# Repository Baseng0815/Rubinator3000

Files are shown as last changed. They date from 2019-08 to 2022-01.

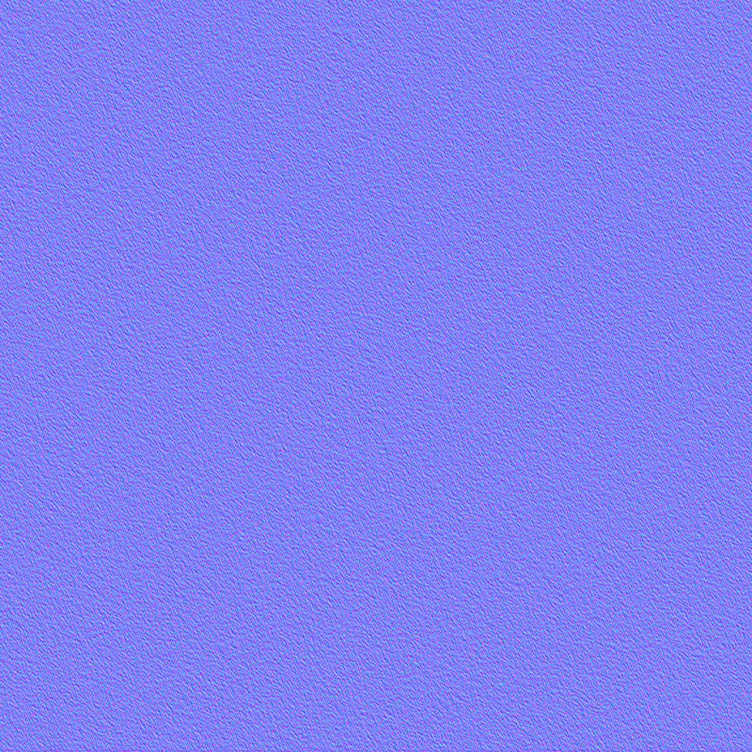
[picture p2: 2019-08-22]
RubinatorTabletView/Assets/Textures/NormalMap.png

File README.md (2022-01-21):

##### GYMNASIUM EDERTALSCHULE, FRANKENBERG-HESSEN

# Jugend forscht 2020

```
Philipp Geil, 19 Jahre
Tim Depner, 18 Jahre
Bastian Engel, 19 Jahre
```
## Das Lösen eines Zauberwürfels

## - der Rubinator3000 -

Mathematik-Informatik
Projektbetreuer: Oliver Blinn, Edertalschule Frankenberg

## Kurzfassung

Bei unserem Projekt “ _Das Lösen eines Zauberwürfels - der Rubinator3000_ ”
versuchten wir, einen verdrehten Zauberwürfel automatisch zu lösen.
Dazu haben wir Software und Hardware entwickelt, die einen Würfel erkennen,
verarbeiten und einen Lösealgorithmus anwenden können.
Anforderungen an die Hardware:
● Drehung jeder Seite des Würfels mit Schrittmotoren
● Elektronik zur Steuerung der Motoren
● Kameras zur Erkennung des verdrehten Würfels
Anforderungen an die Software:
● Auswertung der Kamerabilder und programmiertechnische Darstellung des
Würfels
● Lösealgorithmus entwickeln und Lösezüge berechnen
● Lösezüge am Würfel ausführen
...und natürlich das Vereinen aller Hardware-Komponenten in einer Maschine sowie
dessen Kommunikation mit dem Rechner, auf welchem die Steuerungssoftware
mit grafischer Benutzeroberfläche läuft.

## Erfolge:
1. Preis Regionalwettbewerb 2020
SMA Innovationspreis
Qualifikation Landeswettbewerb, der allerdings aufgrund von Corona abgesagt wurde

## 1. Einleitung

#### 1.1 Wieso einen Zauberwürfel lösen?

Unsere Faszination für Zauberwürfel hat vor ungefähr einem Jahr angefangen, als
wir bei einer extrakurrikularen E-Technik-Vorlesung ein YouTube-Video (Q1) sahen,
in dem jemand einen Zauberwürfel in 4.73 Sekunden löst. Da haben wir uns gefragt,
wie so etwas überhaupt möglich ist. Wir haben es als Kinder selbst probiert und
sogar bis zu drei Seiten gelöst bekommen, aber vollständig klappte es nie. Bei
nachfolgender Recherche im Internet sind wir auf Methoden gestoßen, welche von
sogenannten “Speedcubern” verwendet werden, um den Würfel in einer unglaublich
kurzen Zeit zu lösen.
Vertieft wurde unser Interesse weiter durch die unzähligen Variationen des Würfels.
Abseits der bekannten 3x3-Version ist der Zauberwürfel auch in einigen anderen
Größen von 2x2 bis zu 15x15 erhältlich. Dazu gibt es das Drehpuzzle nicht nur in
Hexaeder-Form, sondern auch in anderen polyedrischen Formen, wie beispielsweise
dem Tetraeder. Einige stellen sich sogar der Herausforderung, den Würfel mit nur
einer Hand, mit den Füßen oder mit verbundenen Augen zu lösen.
Wir selbst schaffen es per Hand, den Zauberwürfel in einer Zeit von circa 45
Sekunden zu lösen. Schaffen wir es, diese Zeit mit unserer Maschine zu
unterbieten?

#### 1.2 Gängige Lösemethoden

Die Lösung des Zauberwürfels erfolgt nicht improvisiert, sondern läuft nach einem
strikten Schema. Dies ist notwendig, um bereits gelöste Teile nicht erneut zu
verdrehen. Manche Teile lassen sich zwar ohne Vorkenntnisse lösen, aber den
Hauptteil löst man mit vorher entwickelten und auswendig gelernten Algorithmen und
Methoden, die den Würfel auf eine bestimmte Art und Weise permutieren.
Die am häufigsten verwendeten Lösemethoden sind zum einen die
“Fridrich”-Methode, welche von Jessica Fridrich entwickelt wurde, und zum anderen
die “Layer-by-Layer”-Methode.
Die Fridrich-Methode enthält viele Algorithmen, die man auswendig lernen muss,
welche jedoch eine kurze Lösezeit garantieren, weshalb sie auch von Speedcubern
verwendet wird.
Die Layer-by-Layer-Methode ist einfacher zu erlernen, erfordert aber mehr Züge, was
die Lösezeit natürlich verlängert.

- Kurzfassung
- 1. Einleitung
      - 1.1 Wieso einen Zauberwürfel lösen?
      - 1.2 Gängige Lösemethoden
      - 1.3 Das Ziel der Arbeit
- 2. Vorgehensweise, Materialien und Methode
      - 2.1 Die Position der Farben auf dem Würfel
      - 2.2 Drehungen der Seiten
      - 2.3 Die Lösung des Zauberwürfels
      - 2.3.1 Das weiße Kreuz
      - 2.3.2 Das F2L
      - 2.3.4 Die letzte Seite
      - 2.4 Die Entwicklung der Software
      - 2.5 Die Entwicklung der Hardware
      - 2.6 Der Bau der Hardware
      - 2.7 Die Digitalisierung des Würfels
- 3. Ergebnisse
      - 3.1 Software
      - 3.2 Hardware
- 4. Ergebnisdiskussion
- 5. Zusammenfassung
- 6. Danksagung
- 7. Quellen- und Literaturverzeichnis

Layer-by-Layer-Methode (Q3)
Ausgang Weißes
Kreuz
Weiße
Ecksteine
Mittlere
Schicht
Gelbes
Kreuz
Gelbe
Ecksteine
Ecksteine
drehen
Fridrich-Methode (Q4)
Ausgang Weißes Kreuz “First two
layers” (F2L)
“Orient last
layer” (OLL)
“Permutate
last layer”
(PLL)
Man erkennt, dass die Fridrich-Methode weniger Schritte benötigt. Dadurch wird sie
jedoch auch komplizierter und schwieriger zu erlernen. Die Layer-by-Layer-Methode
erfordert neun verschiedene Algorithmen, während es bei der Fridrich-Methode
schon 78 sind.

#### 1.3 Das Ziel der Arbeit

Wie schon erwähnt, brauchen wir ganze 45 Sekunden, um den Zauberwürfel per
Hand zu lösen und vergessen häufig Algorithmen. Diesen Problemen wollen wir
durch maschinelles Lösen entgegentreten. Motoren können die Drehungen am
Würfel besser koordinieren als wir mit unseren Händen. Außerdem können Rechner
Algorithmen ohne Probleme speichern und ausführen. Besonders beeindruckt hat
uns dabei der Löseroboter von Ben Katz, welcher in der Lage ist, den Würfel in 0.
Sekunden zu lösen (Q5).
Unser Ziel ist es, den Zauberwürfel innerhalb von 30 Sekunden lösen zu können, d.h.
konkret, eine dafür nötige Farberkennung zu entwickeln, eine entsprechende
Lösesoftware zu schreiben und eine Ansteuerung zu bauen, welche diese
Anforderung erfüllen kann.

## 2. Vorgehensweise, Materialien und Methode

#### 2.1 Die Position der Farben auf dem Würfel

Sei die Menge der Seiten des Würfels und die Menge der Flächen einer Seite.
Damit sind die Positionen der einzelnen Flächen auf dem Würfel bestimmt durch:
Um den Würfel darstellen zu können, müssen die Positionen noch durch die Menge
der Farben des Würfels ergänzt werden:
Damit besteht die Darstellung des Würfels aus einem Array der Länge 6, in welchem
die neun Farbwerte für jede Seite gespeichert sind. Das Programm geht davon aus,
dass sich die orange Fläche links befindet und die weiße Fläche oben. Da die
Implementation des Lösungsalgorithmus leichter fällt, wenn man nicht mit den
einzelnen Flächen arbeitet, sondern jene Flächen zu Steinen zusammenfasst,
welche über die Würfelkanten aneinander grenzen, haben wir uns dazu entschieden,
eine Struktur für die Ecksteine (3 Flächen) und eine für die Kantensteine (2 Flächen)
zu erstellen. In diesen Strukturen werden ein Tupel der Farben des Steines sowie ein
Verweis auf den Würfel, zu dem dieser Stein gehört, gespeichert. Die Steine werden
bei der Initialisierung der Cube-Klasse automatisch aus den vorgegebenen
Positionen erstellt, die für jeden Stein festgelegt sind. Die Steine werden durch ihre
Farben charakterisiert, da die Positionen zum einen durch die Indizes des Arrays
festgelegt sind und es zum anderen für den Lösungsalgorithmus nötig ist, die
Position gewisser Steine anhand der Farben zu identifizieren. Diese Positionen
lassen sich durch einen Vergleich der Farben des Steines mit den vorgegebenen
Steinpositionen bestimmen.

#### 2.2 Drehungen der Seiten

Um den Zauberwürfel nun zu lösen oder zu verdrehen, mussten wir also noch eine
Möglichkeit implementieren, um einzelne Seiten des Würfels im Programm zu
drehen. Eine Drehung wird durch die zu drehende Seite und die Anzahl der
Vierteldrehungen (90°) im Uhrzeigersinn festgelegt.
Jeder Move beschreibt eine bestimmte Permutation des Würfels, da zum einen die
Farben auf der jeweiligen Seite, aber auch teilweise die Farben auf den
angrenzenden Seiten vertauscht werden.

Diese beiden Permutationen können jeweils durch Funktionen beschrieben werden:
Betrachtet man die Drehung einer Seite im Uhrzeigersinn, so lässt sich
bestimmen:
Der Funktionswert von _f_ 1 gibt hierbei die neue Position nach der Drehung an:
Die Funktionswerte von lassen sich nicht allgemein formulieren, da abhängig
von der gedrehten Seite ist. Die Relationen von sind im Programm hinterlegt und
werden auf die entsprechenden Seiten angewendet.

#### 2.3 Die Lösung des Zauberwürfels

#### 2.3.1 Das weiße Kreuz

Das weiße Kreuz wird durch ein Objekt der “CrossSolver”-Klasse gelöst. Dazu wird
zuerst ein Pivotelement festgelegt. Bei diesem Element handelt es sich entweder um
einen weißen Kantenstein, der sich bereits richtig auf der weißen Seite befindet und
bei dem sich die meisten Steine in der gewünschten Position befinden, oder um
einen weißen Kantenstein, der sich mit den wenigsten Zügen in die richtige Position
bringen lässt. Um die Anzahl der Züge zu bestimmen, die benötigt werden, um den
Stein relativ zum Pivotelement richtig auszurichten, gibt es eine Methode, die jeden
Stein bewertet und die Anzahl der Züge zurückgibt. Beim Lösen des weißen Kreuzes
bewertet der “CrossSolver” zuerst für jeden Kantenstein, wie viele Züge jeweils
benötigt werden und löst dann den Kantenstein, für den die wenigsten benötigt
werden. Zum Lösen der einzelnen Steine unterscheidet der “CrossSolver” zwischen
vier verschiedenen Fällen:

1. Der Stein befindet sich mit der weißen Fläche auf der weißen Seite, aberdie
    seitliche Farbe stimmt nicht.
2. Der Stein befindet sich mit der weißen Fläche auf der unteren Seite.
3. Der Stein befindet sich auf der mittleren Ebene, also mit keiner Fläche auf
    der oberen oder unteren Seite.
4. Der Stein befindet sich mit der weißen Fläche auf einer der seitlichen Seiten
    (orange, grün, rot, blau) und mit der anderen Fläche auf der oberen oder
    unteren Seite.
Die einzelnen Fälle werden dann durch vorgegebene Algorithmen gelöst.

#### 2.3.2 Das F2L

Das Lösen des F2L funktioniert analog zum Lösen des weißen Kreuzes. Das
Programm orientiert sich hier nun nicht mehr an nur einem Stein, sondern an jeweils
zwei Steinen, die gelöst werden sollen. Dazu bewertet es wieder jedes Steinpaar und
löst jenes, welches die wenigsten Züge benötigt. Diese Berechnung erfolgt
asynchron, um Rechenzeit zu sparen. Danach wird das Paar mit Hilfe von 13
Algorithmen gelöst.

#### 2.3.4 Die letzte Seite

Für das Lösen der letzten Seite sind im Programm Muster und die dazugehörigen
Zugfolgen hinterlegt (57 OLL und 21 PLL). Die Muster für das OLL beziehen sich nur
auf die Anordnung der gelben Flächen. Dazu wird eine Folge von 9 Bits verwendet,
welche die gelbe Seite repräsentiert, und jeweils vier Folgen von je 3 Bits, welche die
3 Flächen der über die Würfelkanten angrenzenden Seiten repräsentieren. Das
Programm vergleicht dann jegliche Muster mit dem Würfel und kann somit die
Zugfolge angeben. Die PLL-Muster sind etwas komplexer als die OLL-Muster, da das
PLL die einzelnen Farben einbezieht. Dazu wird jeder der vier seitlichen Farben eine
Zahl zugeordnet ((orange, 0), (grün, 1), (rot, 2), (blau, 3)). Im Programm sind dann
die Differenzen zwischen den drei Steinen für alle vier Seiten hinterlegt. Mit diesen
Mustern kann daraufhin die Zugfolge bestimmt werden, die zur Lösung des
Zauberwürfels führt.

#### 2.4 Die Entwicklung der Software

Wir haben mithilfe von Visual Studio Community 2019, einer von Microsoft
entwickelten IDE, programmiert. Das Projektmanagement wird dadurch vereinfacht
und der integrierte Designer erlaubt einfache und gute GUI-Erstellung. Da jeder von
uns schon im Voraus Erfahrung mit dieser Entwicklungsumgebung hatte, mussten
wir uns nicht umstellen und der Entwicklungsprozess konnte sofort starten.
Als Programmiersprache entschieden wir uns für C#, um WPF (Windows
Presentation Foundation) nutzen zu können. Das ist eine GUI-Library, mit der viele
Windows-Programme geschrieben werden. Ein großer Vorteil davon ist, dass das
GUI-Design extern in XAML-Dateien definiert und damit vollständig von der Logik
des Programms abgekoppelt ist. Dies ermöglichte uns, die Arbeit besser aufzuteilen.
So kann ein Programmierer am GUI arbeiten, während ein anderer die Logik dazu
schreibt. Die 2D-und 3D-Ansicht des Würfels erstellten wir mit OpenGL, einer
Graphics-Library, die auch in vielen Computerspielen verwendet wird und sehr
weitreichende Funktionen besitzt.

Da wir zu dritt waren und viele Änderungen parallel zusammenkamen, benötigten wir
ein Versionskontrollsystem, um diese zu verwalten und gegebenenfalls bei Bugs
frühere Versionen wiederherstellen zu können. Entschieden haben wir uns für Git,
welches auch industriell verwendet wird. Damit war es kein Problem mehr, Aufgaben
aufzuteilen und zu synchronisieren.

#### 2.5 Die Entwicklung der Hardware

Das CAD-Modell unseres  _“Rubinator3000”_ haben wir mit dem kostenlosen Programm
“FreeCAD” entworfen, da dieses für unsere Anforderungen genügt und wir unser
Projekt kostengünstig gestalten wollten. Zudem war es uns mit FreeCAD möglich, die
Bauteile in das STL-Format zu exportieren, um sie mit einem 3D-Drucker drucken zu
können. Da unsere Hardware fast ausschließlich aus 3D-Druck Bauteilen besteht,
war diese Funktion sehr hilfreich. Die Schaltpläne für die Ansteuerung der
Schrittmotoren erstellten wir mit Eagle. Eagle bietet zudem die Möglichkeit,
Leiterplatten zu designen, um diese bei einem Leiterplattenhersteller anfertigen zu
lassen.
Die Ansteuerung der Schrittmotoren musste über eine Verstärkerschaltung getätigt
werden. Das lag zum einen daran, dass die Schrittmotoren eine Spannung von 12V
benötigen, während der Arduino nur 5V liefert. Zum anderen wird ein sehr großer
Strom benötigt, um die Magnetfelder innerhalb der Schrittmotoren mit Hilfe von
Spulen zu erzeugen.

#### 2.6 Der Bau der Hardware

Wir haben uns für 3D-gedruckte Bauteile
entschieden, da diese eine höhere Präzision
der Mechanik ermöglichten. Unser erster
Prototyp bestand ausschließlich aus Holz
und es kam aufgrund mangelhafter
Genauigkeit der Mechanik zum
sogenannten “Verkantungsproblem”: Eine
Seite des Würfels verkantete sich nach einer
unvollständigen Drehung. Dieses Problem
lösten wir letztendlich durch die zweite
Version der Hardware und einen anderen Zauberwürfel. Zudem ließen die
verwendeten Miniaturbalg-Kupplungen zu viel Spielraum zu, was zu
Ungenauigkeiten bei den Würfeldrehungen führte. Deshalb ersetzten wir sie durch
Elastomerkupplungen, da diese deutlich genauer sind, wodurch sich der Würfel viel
besser drehen lässt.
Zudem haben wir uns Platinen zur Ansteuerung der Schrittmotoren anfertigen
lassen, da die anfangs selbst gelöteten Platinen teilweise unzuverlässig waren und
sehr viel Platz im Gehäuse in Anspruch nahmen. Hinzu kam noch, dass die selbst
gelöteten Platinen viel Wärme entwickelten, da jede einzelne von ihnen einen

separaten Spannungsregler besaß, der für den Anschluss eines Mikrocontrollers
gedacht war.
Im nebenstehenden Bild ist eine
Schaltung abgebildet, welche zeigt,
wie mithilfe des Transistors (T1) der
Stromkreis der Spule des
Schrittmotors (L1) geschlossen wird^1.
Dadurch wird es möglich, dass Strom
fließen kann, welcher das
magnetische Feld im Schrittmotor
erzeugt. Der Basiswiderstand (R1)
dient zur Begrenzung des
Basisstroms des Transistors, da der
Ausgang des Arduino einen Strom
von maximal 40mA zur Verfügung
stellt.
Wir ließen die Bodenplatte bei der Firma Viessmann drucken, weil diese für unseren
3D-Drucker zu groß war. Sie stellte uns für diesen Druck einen besseren 3D-Drucker
zur Verfügung. Nach dem Druck haben wir sie auf eine solide Holzbox gesetzt,
welche auch die Elektronik enthält. Dadurch wird Stabilität garantiert und die Motoren
können passend positioniert werden.

#### 2.7 Die Digitalisierung des Würfels

Unsere erste Methode zur Digitalisierung des Würfels sah folgendermaßen aus:

(^1) Die Freilaufdiode wurde zur Vereinfachung der Schaltung weggelassen

Wir lasen jede einzelne Seite mit der Kamera eines Smartphones ein, um daraus den
Würfel digital zusammensetzen zu können. Dafür haben wir eine Android-App in der
Programmiersprache Java geschrieben.
Ein Computer – also auch das Smartphone, welches wir benutzen – stellt Farben im
RGB-Format dar. Anhand dieser Werte werden die einzelnen Würfel-Farben
(Orange, Weiß, Grün, Gelb, Rot und Blau) auch unterschieden.
Um sich auch wechselnden Lichtverhältnissen anpassen zu können, war es nötig zu
Beginn Referenz-RGB-Werte festzulegen, anhand welcher die App die Farben
unterschied.
Im nächsten Schritt hielten wir die Handykamera vor jede Würfelseite. Die App las
die RGB-Werte der einzelnen Flächen aus und ordnete ihnen anhand der anfangs
eingelesenen Referenz-RGB-Werten die entsprechende Farbe zu.
Sobald die App eine Würfelseite eingelesen hatte, schickten wir dessen Farben über
ein WLAN-Netzwerk an jenen Laptop, auf welchem das Hauptprogramm lief.
Nachdem wir auf diese Weise alle sechs Seiten eingelesen und an den Laptop
geschickt hatten, könnte dieser daraus den Würfel digital zusammensetzen.
Die zweite Version unseres Projekts brachte auch ein Upgrade in der Farberkennung
mit sich. Anstatt mit einer Handy-App jede Seite einzeln einzulesen, brachten wir vier
stationäre USB-Kameras an der Maschine an, mit welchen wir die RGB-Werte der
einzelnen Flächen des Würfels automatisch einlesen. Dies beschleunigt den Prozess
der Digitalisierung des Würfels natürlich enorm.
Auch an der Erfassung und Verarbeitung der eingelesenen RGB-Werte haben wir
Änderungen vorgenommen:
Für jede einzelne Fläche des Würfels
legen wir eine Position auf einem der 4
Kamera-Streams fest, an welcher die
RGB-Werte der jeweiligen Fläche
ausgelesen werden sollen. Da die 8
Mittelsteine des Würfels ihre Position
während des Drehen nie verändern,
werden deren RGB-Werte gar nicht mehr
eingelesen.
So lesen wir alle RGB-Werte an den 48
Positionen ein und berechnen die
jeweilige Wahrscheinlichkeit dafür, dass
die jeweiligen RGB-Werte zu einer orangen, weißen, grünen, gelben, roten oder
blauen Fläche gehören.
Die 8 Flächen an den Positionen mit den höchsten Orange-Wahrscheinlichkeiten
bestimmen wir als orange Flächen. So gehen wir die restlichen 5 Farben ebenfalls
durch und haben zum Schluss 8 Flächen von jeder Farbe, mit welchen wir wiederum
den Würfel digital darstellen.

Durch dieses Verfahren wird die Farberkennung viel präziser, da wir davon
ausgehen, dass wir genau 8 Flächen von allen Farben haben.
Ein Problem, welches wir bei der Farberkennung hatten war Folgendes:
Aufgrund der sehr glatten Oberfläche der Würfelflächen, spiegelten diese das
Umgebungslicht teilweise gebündelt direkt in eine der Kameralinsen. Dadurch war im
Kamerabild nicht die entsprechende Farbe der Seite zu sehen, sondern ein helles,
weißliches Leuchten. Dies verfälschte die RGB-Werte, welche für die dazugehörige
Fläche eingelesen wurden. Eine eigentlich blaue Fläche erschien somit
unerwünschterweise weiß. Wir haben dieses Problem gelöst, indem wir einen
Vorhang über die ganze Maschine gehängt haben, um den Spiegelungseffekt zu
minimieren. Damit wir jedoch überhaupt noch etwas mit den Kameras sehen können,
haben wir zusätzlich LEDs direkt in die Maschine gebaut, welche den Würfel mit
diffusem Licht bescheinen.
Dies soll jedoch nur vorübergehend die Lösung des Problems sein, da das Abdecken
und das Entfernen der Abdeckung recht viel Zeit braucht. Für die Zukunft planen wir,
nicht absolute Positionen, an welchen die Farben des Würfels ausgelesen werden,
zu benutzen. Stattdessen soll das Programm mittels Konturerkennung selbst
herausfinden, wo sich auf dem entsprechenden Kamerabild die einzelnen
Würfel-Flächen befinden, von welchen das Programm daraufhin die entsprechenden
Farben ausliest. Hierbei könnten wir zu helle Pixel aussortieren, wodurch das
“Spiegelungs-Problem” gelöst würde. Erste Tests in separat von uns programmierten
Anwendungen liefern vielversprechende Ergebnisse. Jetzt gilt es noch, die neue
Farberkennung in das Hauptprogramm zu implementieren.

## 3. Ergebnisse

#### 3.1 Software

Wir haben mithilfe der vorgestellten Vorüberlegungen und Methoden das
Hauptprogramm fertiggestellt, welches den Würfel lösen und die Lösealgorithmen
über eine serielle Schnittstelle an den Arduino schicken kann.
Die Effizienz der Algorithmen lässt sich an folgendem Graph ablesen:
Für jede Verdrehungsanzahl machten wir 30
Testdurchgänge, woraufhin daraus der
Mittelwert gebildet wurde. Die
Schwankungen lassen sich dadurch erklären,
dass nur ein einziger zusätzlich ausgeführter
Algorithmus mehrere Züge enthält und
dadurch das Ergebnis stark beeinflusst
werden kann.
Es ist zu erkennen, dass unsere Lösung ab
vier Verdrehungen erheblich mehr Züge
benötigt. Ab sechs Verdrehungen pendelt sich
die Anzahl der Lösezüge auf ungefähr 65 ein.
Die Schrittmotoren lassen sich mit 360° pro Sekunde drehen, was zwei Zügen
entspricht. Daher ist eine theoretische Lösezeit von ca. 15 Sekunden erreichbar, die
aber durch Ausnahmefälle wie zum
Beispiel die Doppeldrehung einer
Seite oder dem  _Multiturning_
Schwankungen unterliegt.
Außerdem ist zu erkennen, dass
der Zugzuwachs am stärksten vom
FTL beeinflusst wird, wobei die
OLL- und PLL-Algorithmen gegen
Ende weniger beitragen. Das Kreuz
hat kaum Einfluss.
Die grafische Oberfläche des
Programms enthält alle nötigen
Kontrollelemente, so zum Beispiel
das Verdrehen oder Lösen des Würfels oder Debug-Fenster zum Beheben von
fehlerhaften Algorithmen und Mustern. Dadurch können wir leicht und ohne

ständiges Überlegen Einstellungen ändern und Tests durchführen. Das ist zum
Beispiel besonders relevant für die Verbindung zum Mikrocontroller, da diese über
einen sich ändernden COM-Port stattfindet, welchen man anfangs auswählen muss.

#### 3.2 Hardware

Der Arduino wartet nach dem Verbinden mit dem Programm auf die Befehle und
führt diese aus. Er ist nötig, da die Schrittmotoren nicht direkt an den Computer
angeschlossen
werden können.
Zudem benötigen die
Schrittmotoren sehr
viel Strom. Deshalb ist
es notwendig, für
jeden Schrittmotor
eine Schaltung zu
bauen, die genug
Strom liefern kann,
um den Würfel zu
drehen. Anfangs
hatten wir die Motoren
nach einer Drehung
nicht abgeschaltet und
so entstand das
Problem, dass alle
inaktiven Motoren zu

viel Strom verbrauchten und somit nicht genug Drehmoment bereitstand, um den
Würfel zu drehen. Dieses Problem haben wir softwaretechnisch gelöst, indem wir
den Strom der Motoren nach jeder Drehung abschalteten und so der komplette
Strom des Netzgerätes für einen oder bei Multiturns zwei Motoren bereitsteht.

## 4. Ergebnisdiskussion

Unser  _“Rubinator3000”_ ist noch nicht das perfekte Ergebnis jahrelanger Forschung,
aber es kann sich trotzdem sehen lassen.
Wie anfangs bereits erwähnt, kam uns die Idee zum Bau einer solchen Maschine, bei
einer extrakurrikularen E-Technik-Vorlesung im Rahmen der Young Engineer
Academy (YEA). Wir haben dort überlegt, was wir als unser Abschlussprojekt bei der
YEA realisieren könnten. Da wir noch viel Zeit hatten, bis das Projekt vorgestellt
werden sollte, entschieden wir uns nach einigen Suchanfragen im Internet für den
Bau eines doch recht aufwendigen Zauberwürfel-Lösers. Einige weitere
Kursteilnehmer, welche sich ebenfalls für den Zauberwürfel begeistern, unterstützten
unsere Idee.
Anfangs schien unsere Aufgabe recht simpel, da man lediglich 6 Schrittmotoren
benötigte, die die Seiten des Zauberwürfels drehen sollten.
Bereits in den nächsten Wochen (Januar 2019) starteten wir mit der
Programmierung. Der eigentliche Bau der ersten Maschine begann dann Ende April
2019 und pünktlich zum Präsentationstermin am 28. Juni vollendeten wir die erste
Version der Hardware. Bis dahin hatten wir während der Schulzeit schon dutzende
Freistunden in unser Projekt investiert, da die Umsetzung des Projekts dann doch
komplizierter war, als wir zunächst vermutet hatten. Vor allem die Drehung des
Würfels machte uns zu schaffen, da die Hardware zu ungenau war und der Würfel
sich deshalb immer wieder verkantete. Dies war aber letztendlich nicht das größte
Problem, welches wir bei der Präsentation hatten.
Auf der Bühne scheiterte die Vorführung unserer Maschine am Lösen des
Zauberwürfels durch das Programm.
Also entschlossen wir uns, in den Sommerferien das Programm zu überarbeiten. Da
der bestehende Code mittlerweile sehr unübersichtlich war und wir nicht genau
wussten, wo die einzelnen Fehler lagen, entschlossen wir uns dazu, das Programm
von Grund auf neu zu entwickeln. Wir besaßen bereits das Vorwissen aus dem
ersten Versuch , weshalb uns die Entwicklung der zweiten Maschine leichter fiel.
Aufgrund der Verkantungen des Würfels kam uns die Idee, die Teile der Hardware,
welche eine hohe Genauigkeit erforderten, mit dem 3D-Drucker zu fertigen, da dieser
viel genauere Ergebnisse liefert als das Aussägen aus Holz. Zudem haben wir neue
Kupplungen eingebaut, die zur Erhöhung der Genauigkeit beitrugen.

Das Projekt erschien uns auf den ersten Blick leicht, aber es gab viele Faktoren, die
wir nicht berücksichtigt hatten. Darunter fiel zum Beispiel das Einlesen des Würfels,
das Bauen der Hardware mit einer hohen Genauigkeit und vieles andere.
Die Software könnte noch verbessert werden, indem man beispielsweise eine andere
Methode zum Lösen des Würfels verwendet, die weniger Züge benötigt. Diese
Verbesserung würde das maschinelle Lösen auch erheblich beschleunigen, da sich
die Motoren dadurch weniger drehen müssten.
Zudem könnte man auch Motoren verwenden, die sich schneller ansteuern lassen,
welche ebenfalls das Lösen beschleunigen würden.
Wir hatten während der Entwicklung die Idee das Hauptprogramm auf einem
Raspberry Pi laufen zu lassen, da dieser den Computer ersetzen würde, der die
Lösung berechnet. Diese Idee verwarfen wir aber schnell, da wir schon angefangen
hatten, die Software auf dem .NET Framework von Microsoft für Windows zu
entwickeln, während der Raspberry auf einem linuxbasierten Betriebssystem läuft.
Der Ansatz könnte aber in der Zukunft realisiert werden.
Auch die Ansteuerung der Motoren hat uns Probleme bereitet, da wir eine eigene
Platine entwickelt und einen Mikrocontroller programmiert haben. Dieser ist jedoch
beim Debuggen der Software durch eine Überspannung kaputt gegangen und wir
mussten ihn durch einen Arduino ersetzen.

## 5. Zusammenfassung

Zusammenfassend lässt sich sagen, dass unser Projekt noch viele
Erweiterungsmöglichkeiten bietet. Es könnten beispielsweise noch LEDs eingebaut
werden, die für eine bessere Beleuchtung des Würfels bei schlechten
Lichtverhältnissen sorgen.
Unser Ziel, dass unsere Maschine weniger Zeit zum Lösen des Würfels benötigt als
wir selbst per Hand, hat das Projekt noch nicht ganz erreicht. Es befindet sich aber
auf einem guten Weg zu einer Lösung, die unseren ursprünglichen Anforderungen
gerecht wird. Dies könnte durch weitere Verbesserungen der Hard- und Software
erreicht werden.
Das Projekt  _“Rubinator3000”_ hat zwar nur einen kleinen Nutzen für die Allgemeinheit,
aber es hat uns geholfen, unsere Kompetenzen im Bereich der Programmierung und
der Entwicklung von Hardware zu erweitern. Zudem haben wir die Erfahrung
gemacht, dass Dinge und Ideen oft einfacher erscheinen, als sie es eigentlich sind.
Es lohnt sich also, zuerst darüber nachzudenken, wie man sie angeht und realisiert.
Zuletzt durften wir die Erfahrung machen, was man mit Teamwork alles erreichen
kann. Während des Entwicklungsprozesses haben sich alle Team-Mitglieder nur auf

jeweils ein Teilgebiet spezialisiert. Trotzdem können wir durch unsere gelungene
Zusammenarbeit nun einen voll funktionsfähigen Zauberwürfellöser präsentieren.

## 6. Danksagung

Abschließend bedanken wir uns für jegliche Unterstützung während der Umsetzung
unseres Projekts.
Exemplarisch möchten wir hier die Fachschaft Physik der Edertalschule nennen,
welche uns bei Fragen in der Umsetzung beriet und uns kostenlos über einen
längeren Zeitraum den Zugang zu ihrem Werkraum gewährte, in welchem wir unsere
Maschine entwickeln und anfertigen konnten. Zudem danken wir unseren
Mitschülern der Young Engineer Academy, die uns beim Bau der ersten Version des
“Rubinator3000” unterstützt haben.
Darüber hinaus geht ein riesiges Dankeschön an die Viessmann Group, welche uns
finanziell bei der Anfertigung der Hardware unterstützte. Zusätzlich ermöglichte sie
uns die Teilnahme an der Young Engineer Academy, durch welche wir essentielle
Grundkenntnisse und letztendlich auch die Idee für dieses Projekt bekommen haben.

## 7. Quellen- und Literaturverzeichnis

##### Q1: 04.01.2020 16: https://www.youtube.com/watch?v=KfpJZHP6DLA
##### Q2: 04.01.2020 17: https://speedcube.de/
##### Q3: 04.01.2020 17: https://ruwix.com/the-rubiks-cube/how-to-solve-the-rubiks-cube-beginners-method/
##### Q4: 04.01.2020 17: https://ruwix.com/the-rubiks-cube/advanced-cfop-fridrich/
##### Q5: 04.01.2020 17: https://www.youtube.com/watch?v=nt00QzKuNVY
##### Q6: 14.01.2020 19: https://www.arduino.cc/en/Tutorial/DigitalPins

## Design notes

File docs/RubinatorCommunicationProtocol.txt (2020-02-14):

A0xbyte		meaning

state:
0xA1		disconnect
0xA2		connect
0xA3		solve
0xF1		disconnected
0xF2		connected
0xF3		solved

bluetooth:
0x00		transmit cube to client
0x01		transmit cube to server
0x30		solve cube
0x31		shuffle cube

LED control:
0x41		LED's down          0b0100_0001
0x43		LED's up            0b0100_0010
0x44		LED stripes         0b0100_0100

errors:
0xB0		error
0xB1		error not connected
0xB2		error not valid

moves:
0x02		Move 'L'
0x03		Move 'Li'
0x04		Move 'U'
0x05		Move 'Ui'
0x06		Move 'F'
0x07		Move 'Fi'
0x08		Move 'D'
0x09		Move 'Di'
0x0A		Move 'R'
0x0B		Move 'Ri'
0x0C		Move 'B'
0x0D		Move 'Bi'

parallel moves:
0x10		Move 'LR'		0b0001_0000
0x11		Move 'LRi'		0b0001_0001 
0x12		Move 'LiR'		0b0001_0010
0x13		Move 'LiRi'		0b0001_0011
0x14		Move 'UD'		0b0001_0100
0x15		Move 'UDi'		0b0001_0101
0x16		Move 'UiD'		0b0001_0110
0x17		Move 'UiDi'		0b0001_0111
0x18		Move 'FB'		0b0001_1000
0x19		Move 'FBi'		0b0001_1001
0x1A		Move 'FiB'		0b0001_1010
0x1B		Move 'FiBi'		0b0001_1011

0x20 + "Move"	Move "Move" done

states:

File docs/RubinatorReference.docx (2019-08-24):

Rubinator

Inhalt:

1. Das weiße Kreuz
2. FTL
1. Das weiße Kreuz
  1.1. Mögliche Stellung der weißen Kantensteine
1. Kantenstein in der gelben Ebene
  a. Weiße Fläche zeigt nach oben (gelbe Seite)
  b. Weiße Fläche zeigt zur Seite
2. Kantenstein in der mittleren Ebene
  a. Weiße Fläche zeigt zur Seite
3. Kantenstein in der weißen Ebene
  a. Weiße Fläche zeigt nach unten (weiße Seite)
  b. Weiße Fläche zeigt zur Seite

Daraus ergeben sich 5 mögliche Fälle, die auftreten und unterschiedlich gelöst werden.

  1.2. Lösung der Stellungen
    1.2.1. Kantenstein auf der gelben Ebene
  a. Weiße Fläche zeigt nach oben
1. Den weißen Kantenstein solange auf der gelben Ebene bewegen (U) bis er die entsprechende Seite erreicht hat.
2. Die Seite, auf der der Kantenstein eingesetzt wird, wird zwei Mal gedreht, sodass der weiße Kantenstein auf der weißen Ebene ist.
  b. Weiße Fläche zeigt zur Seite
1. Die gelbe Ebene solange drehen bis der weiße Kantenstein die entsprechende Seite erreicht hat.
2. Die entsprechende Seite um 90° im Uhrzeigersinn drehen und die weiße Seite danach ebenfalls im Uhrzeigersinn drehen.
3. Die benachbarte Seite gegen den Uhrzeigersinn drehen, um den Kantenstein auf die weiße Ebene zu befördern.
4. Die weiße Ebene gegen den Uhrzeigersinn zurück in die ursprüngliche Position drehen.
1. Weißer Kantenstein in der mittleren Ebene
1. Die weiße Ebene so drehen, dass der Kantenstein eingesetzt werden kann
2. Den Kantenstein einsetzen
3. Die weiße Ebene zurück in die ursprüngliche Position drehen
2. Weißer Kantenstein in der weißen Ebene
  a. Weiße Fläche zeigt nach unten
1. Seitliche Seite im Uhrzeigersinn drehen
2. Die weiße Ebene ausrichten
3. Den Kantenstein einsetzen
4. Die weiße Ebene zurückdrehen
  b. Weiße Fläche seitlich
1. Seitliche Seite drehen
2. Die weiße Ebene ausrichten
3. Den Kantenstein einsetzen
4. Die weiße Ebene zurückdrehen
2. FTL
  2.1. Weißen Eckstein in einen Slot positionieren

Der Stein wird in den richtigen Slot gesetzt, wenn er in einem Zug dort positioniert werden kann. In dem anderen Fall wird er in einen beliebigen Slot positioniert und danach mit dem Kantenstein gepaart, bevor er dann in den richtigen Slot gesetzt wird.

Mögliche Fälle:

1. Der Eckstein und der entsprechende Kantenstein sind bereits gepaart
2. Die weiße Fläche des Ecksteins zeigt zur Seite
3. Die weiße Fläche zeigt nach oben
  2.2. Lösung
    2.2.1. Fall 1

Die beiden Steine werden in den richtigen Slot eingesetzt

    2.2.2. Fall 2
1. Weiße Fläche wird auf die Seite gedreht, die der Gegenfarbe der seitlichen Seite des Ecksteins entspricht.
2. Die Seite der seitlichen Farbe wird gedreht (weiße Fläche auf Tile 8 → gegen den Uhrzeigersinn, weiße Fläche auf Tile 6 → im Uhrzeigersinn)
3. Gelbe Seite drehen (weiße Fläche auf Tile 6 → gegen den Uhrzeigersinn, weiße Fläche auf Tile 8 → im Uhrzeigersinn)
4. Die Seite der seitlichen Farbe zurückdrehen
    2.2.3. Fall 3

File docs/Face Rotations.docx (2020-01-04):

Face Rotations

L-Move

f_0 :{{t∈(U∩{0;3;6})}→Ft⟼t

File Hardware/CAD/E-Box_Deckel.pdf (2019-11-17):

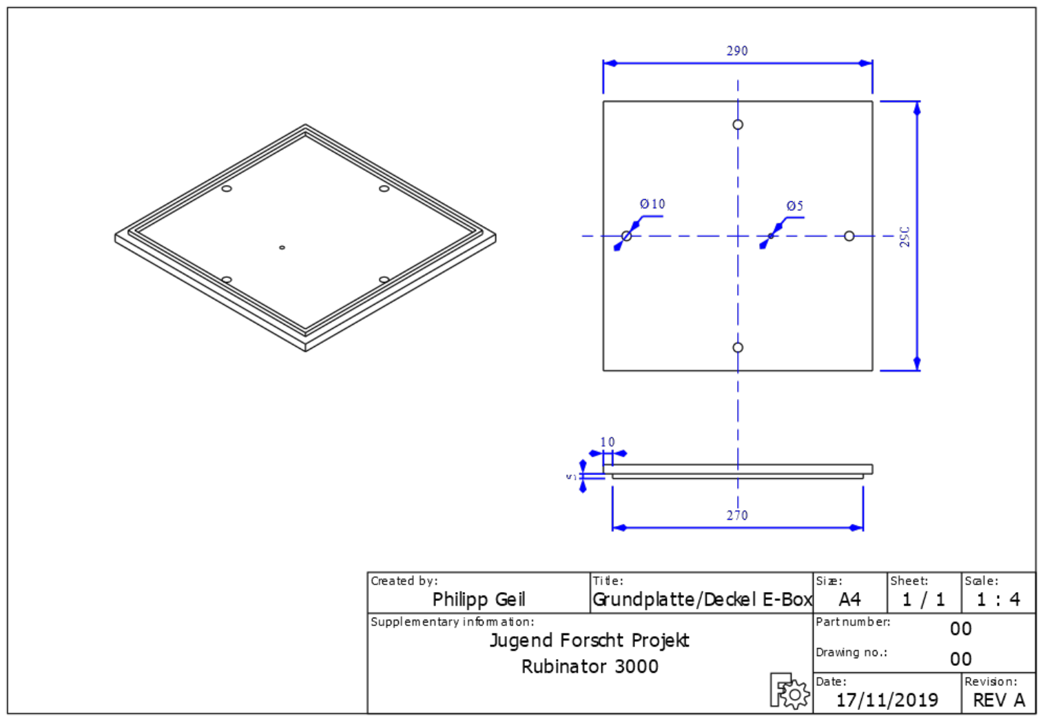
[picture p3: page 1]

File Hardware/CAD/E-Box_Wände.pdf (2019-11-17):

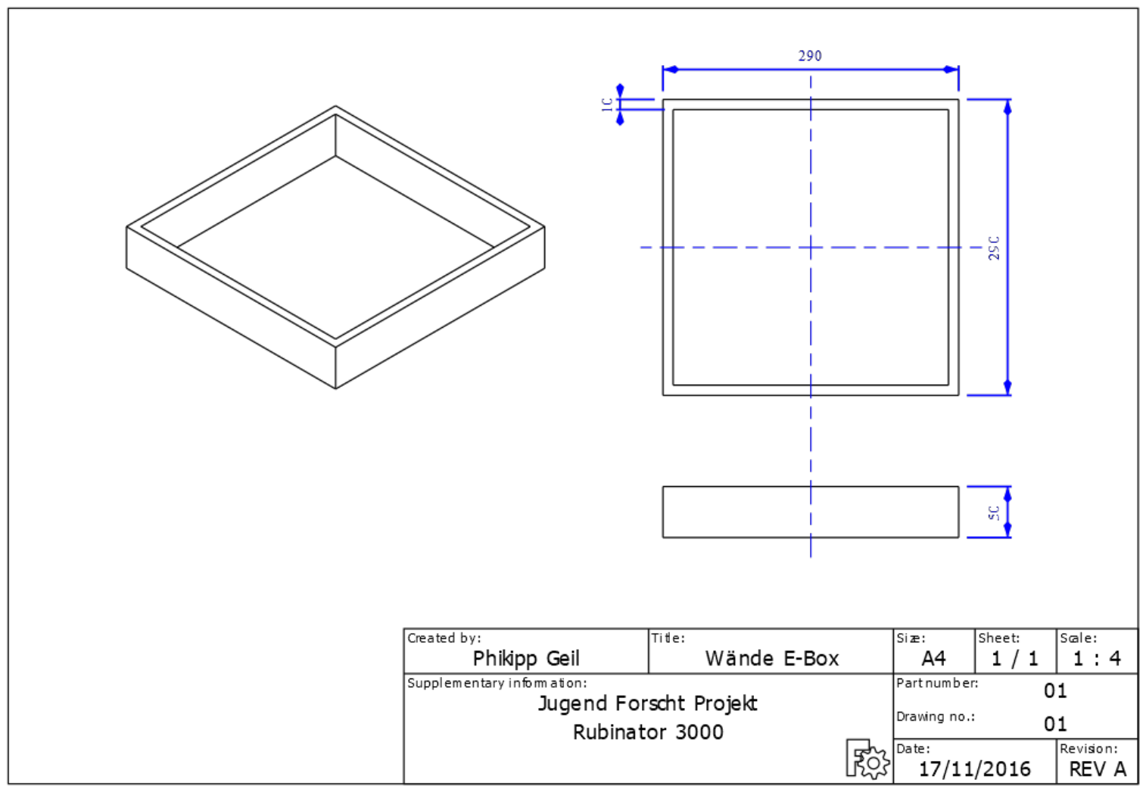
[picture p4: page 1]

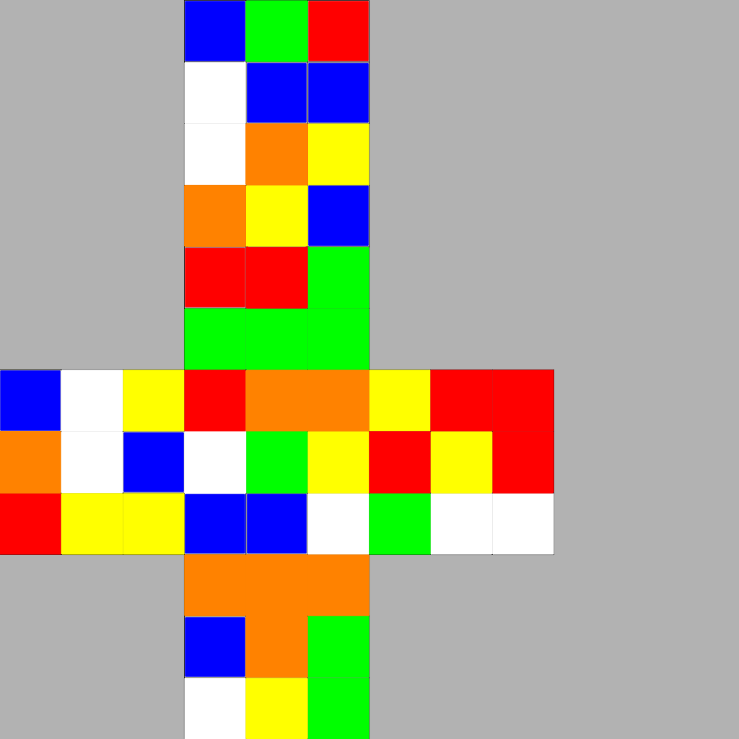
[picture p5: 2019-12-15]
Hardware/CAD/blender/CubeTex.png

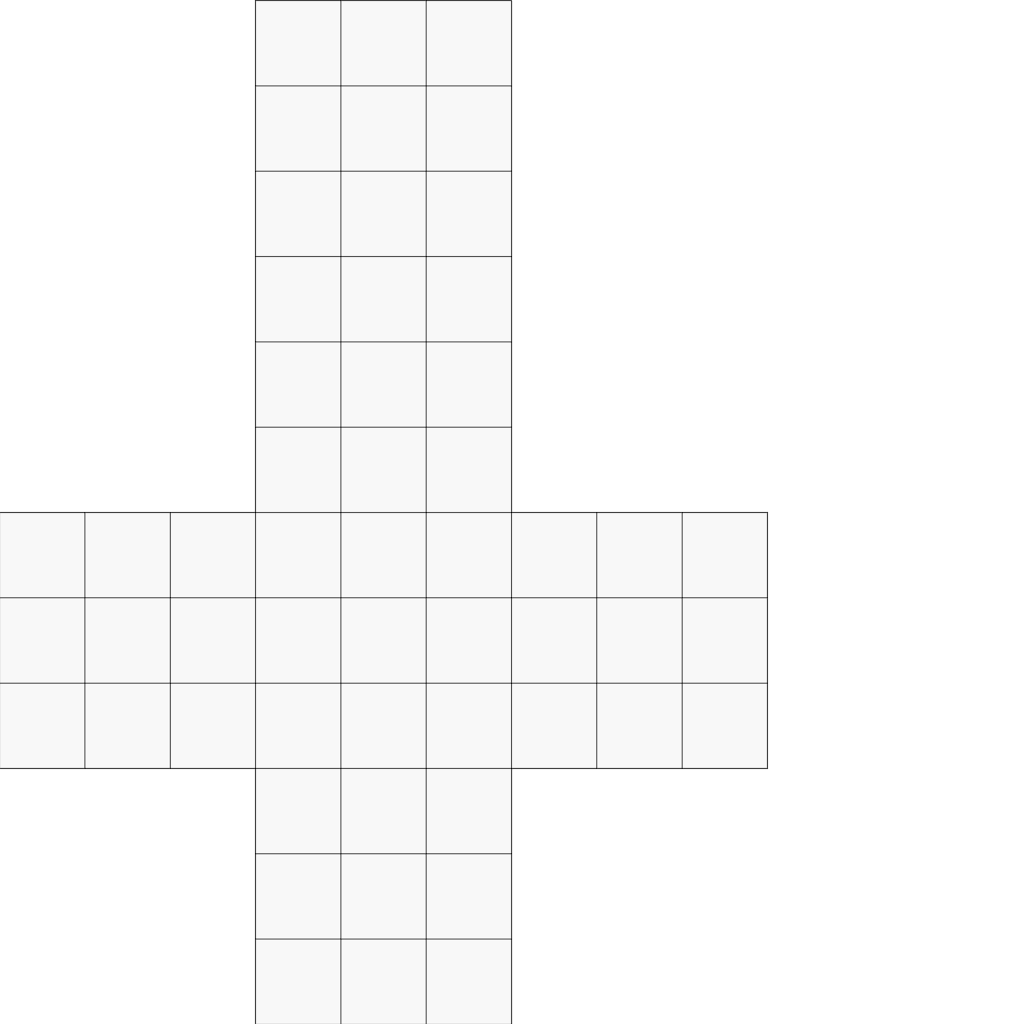
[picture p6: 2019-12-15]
Hardware/CAD/blender/uvs.png

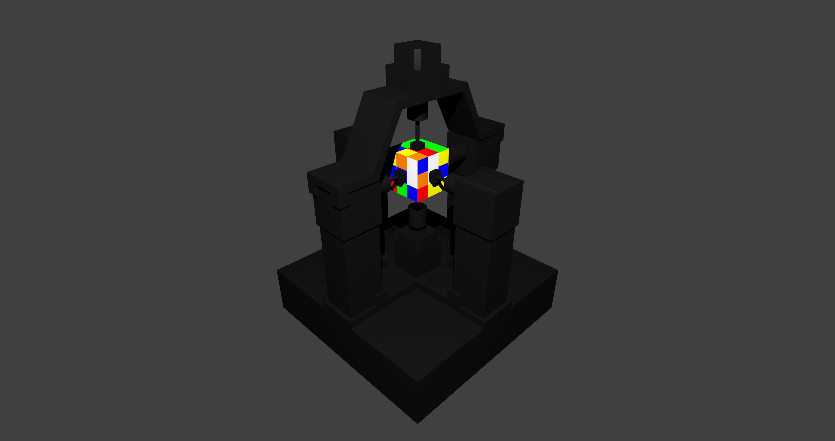
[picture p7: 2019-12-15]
Hardware/CAD/blender/Rubinator3000.png

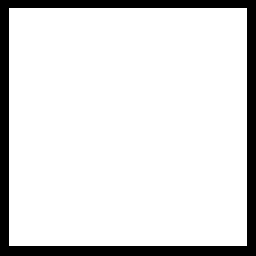
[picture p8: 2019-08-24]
RubinatorTabletView/Assets/Textures/BlendFrameThick.png

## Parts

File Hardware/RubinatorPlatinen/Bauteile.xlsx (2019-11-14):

Teil | Anzahl | Vorhanden
ATMega16-P + IC-Sockel | 1 | 1
Festspannungsregler 5V | 1 | 1
Festspannungsregler 3.3V | 1 | 1
Widerstände
100Ω | 1 | 1
200Ω | 30 | 30
PinHeader (female)
1x4 | 6 | 6
2x8 | 1 | 1
2x10 | 1 | 1
PinHeader (male)
2x10 | 1 | 1
Dioden 1N4446 | 24
Dioden 1N4148 | 2
Transistoren NPN groß | 24 | 24
Transistoren NPN klein | 3 | 3

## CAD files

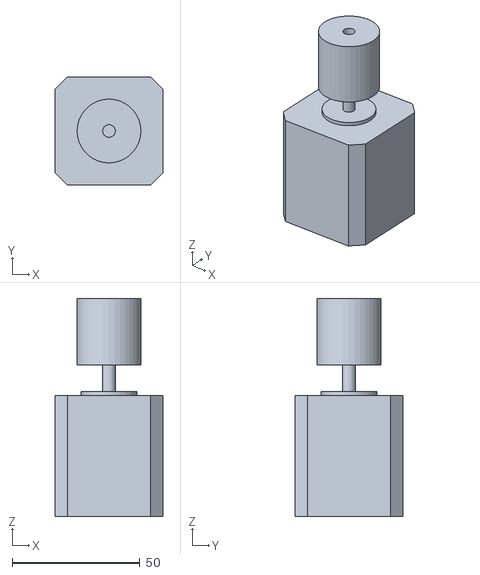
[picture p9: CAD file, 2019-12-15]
Hardware/CAD/AntriebUnten.stl
42.5 x 42.5 x 85.4

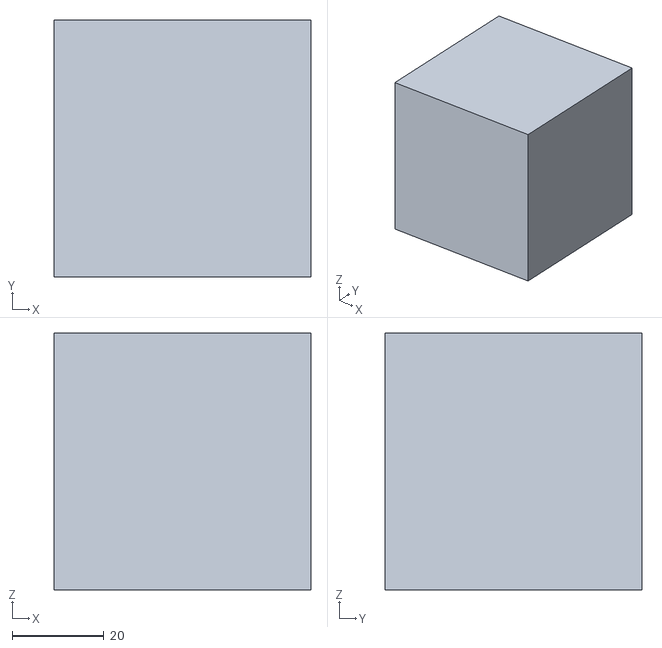
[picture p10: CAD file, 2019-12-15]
Hardware/CAD/blender/Würfel.stl
56.0 x 56.0 x 56.0

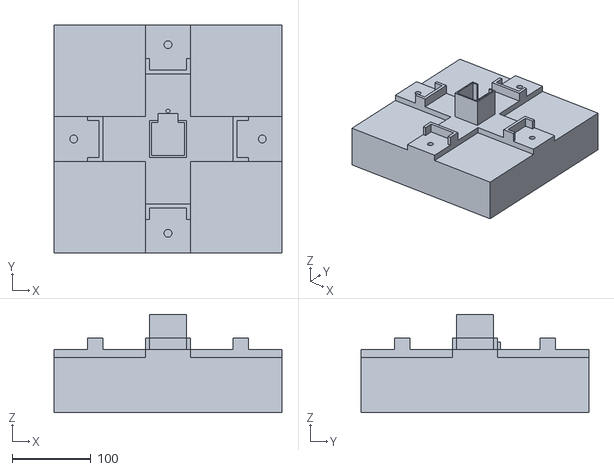
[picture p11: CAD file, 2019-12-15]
Hardware/CAD/blender/Elektrobox.stl
290.0 x 290.0 x 125.0

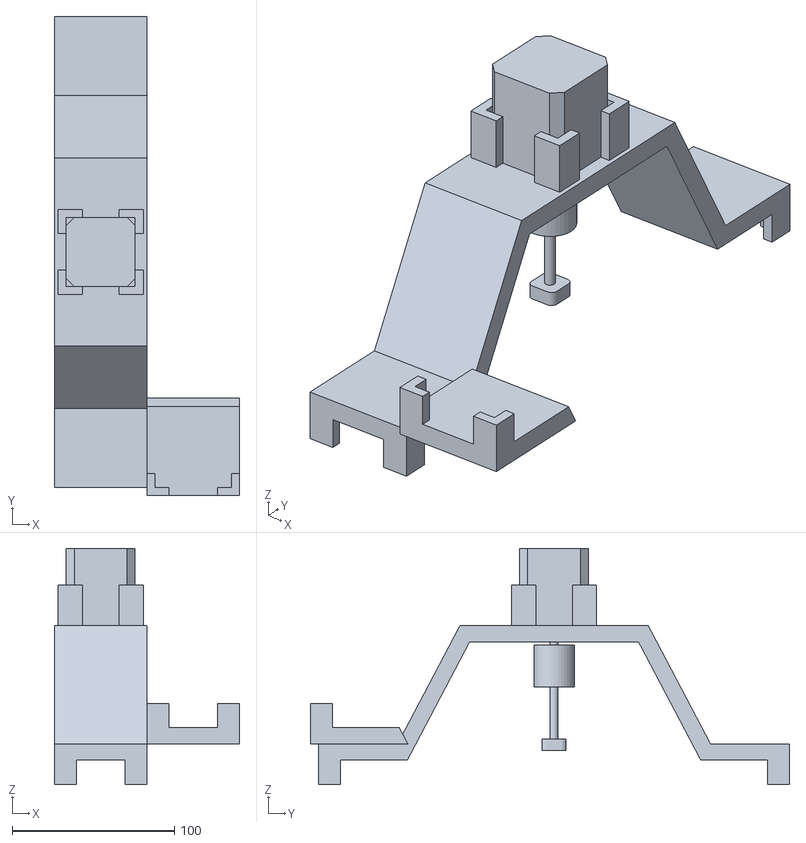
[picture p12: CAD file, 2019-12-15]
Hardware/CAD/blender/HalterungOben.stl
114.0 x 295.0 x 145.2

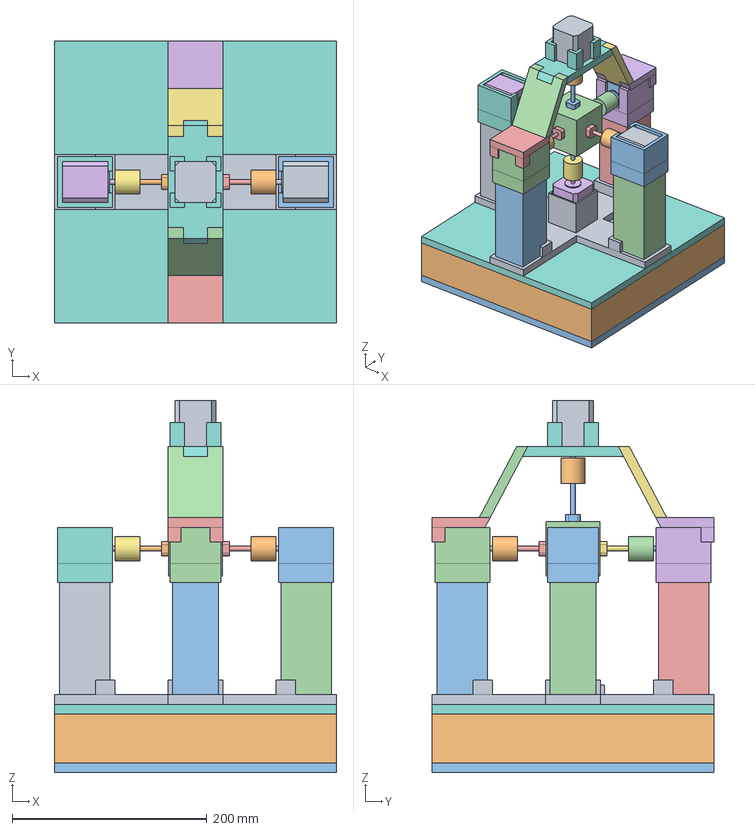
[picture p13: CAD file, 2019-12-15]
Hardware/CAD/Rubinator3000.FCStd
290.0 x 290.0 x 382.3 mm
MotorVorne
KupplungVorne
StützeVorne
MotorufsatzVorne
VerbindungVorne
MotorUnten
KupplungUnten
VerbindungUnten
MotorRechts
KupplungRechts
MotorufsatzRechts
StützeRechts
VerbindungRechts
MotorLinks
KupplungLinks
MotorufsatzLinks
StützeLinks
VerbindungLinks
MotorHinten
KupplungHinten
StützeHinten
MotorufsatzHinten
VerbindungHinten
Deckel
Bodenplatte
Wände
Grundplatte
MotorOben
KupplungOben
VerbindungOben
Würfel

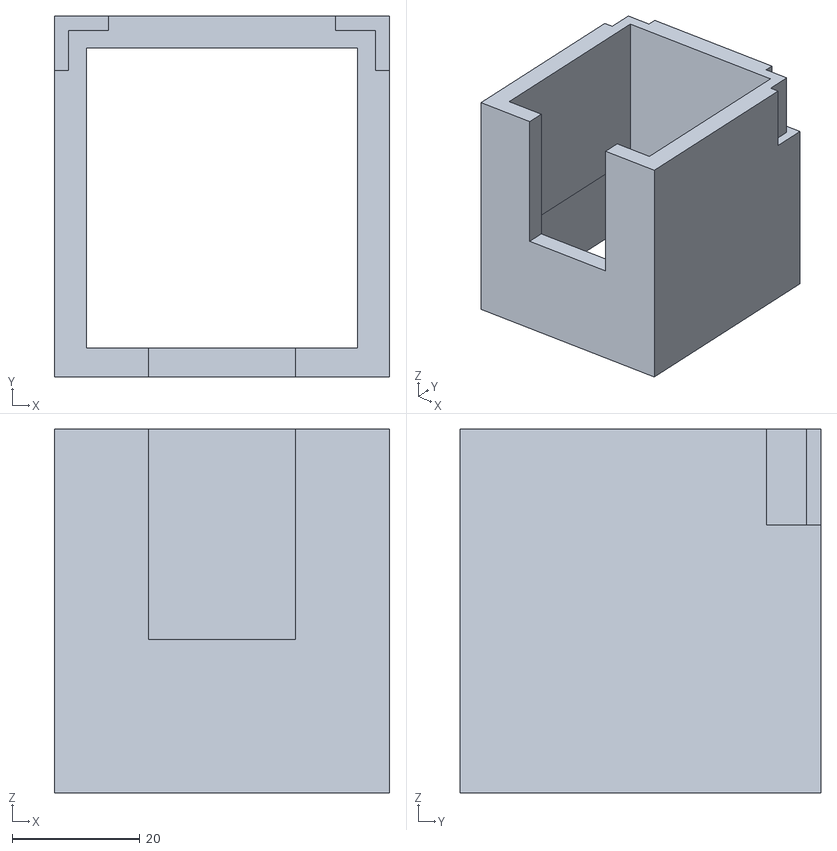
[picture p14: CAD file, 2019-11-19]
Hardware/CAD/AufsatzMotorAussparung.stl
52.5 x 56.5 x 57.0

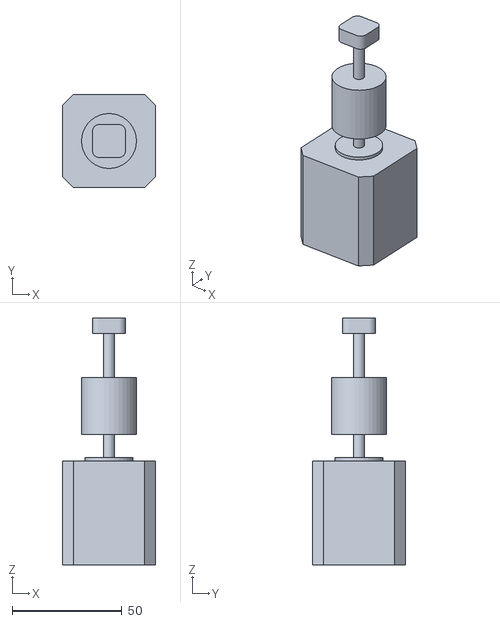
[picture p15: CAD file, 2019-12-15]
Hardware/CAD/blender/Antriebuten.stl
42.5 x 42.5 x 112.4

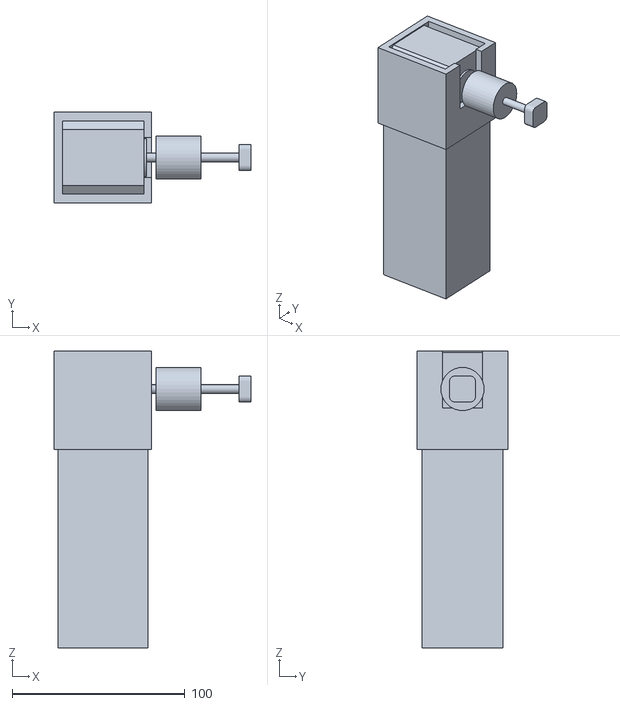
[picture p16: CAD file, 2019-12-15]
Hardware/CAD/blender/TurmLinks.stl
114.0 x 52.5 x 172.0

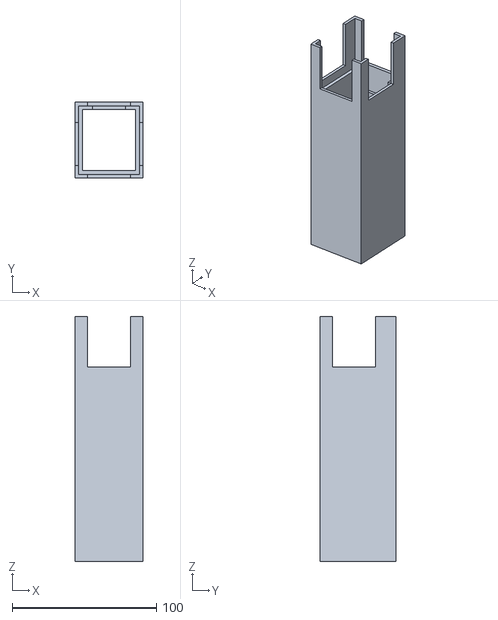
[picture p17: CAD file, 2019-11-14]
Hardware/CAD/Stütze.stl
47.0 x 52.4 x 170.0

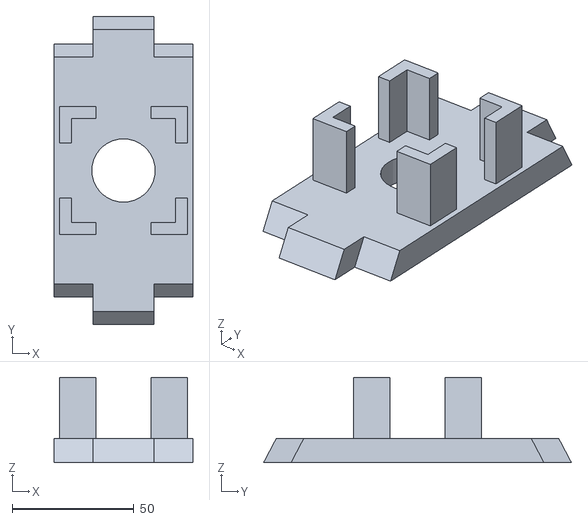
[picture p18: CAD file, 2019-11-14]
Hardware/CAD/HalterungTeil3.stl
57.0 x 126.4 x 35.0

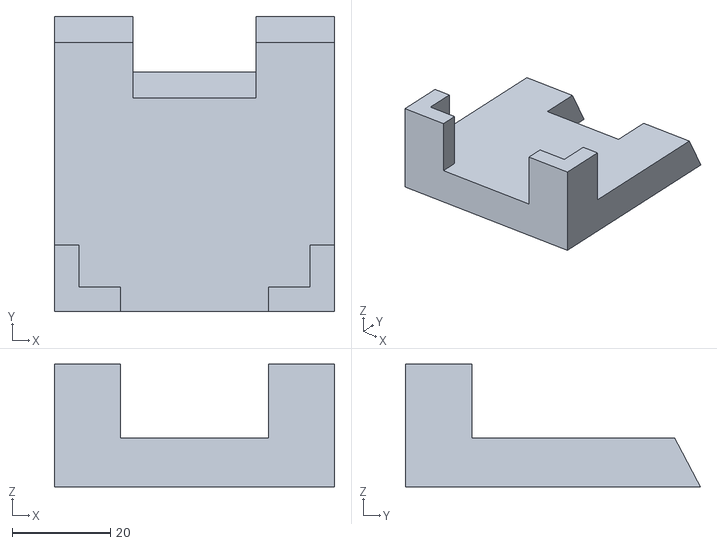
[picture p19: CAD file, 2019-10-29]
Hardware/CAD/HalterungTeil1.stl
57.0 x 60.0 x 25.0

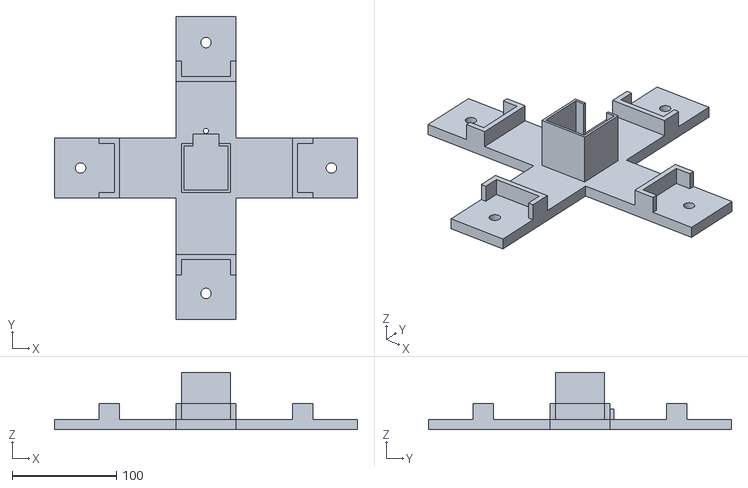
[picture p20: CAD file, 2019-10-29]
Hardware/CAD/Bodenplatte.stl
290.0 x 290.0 x 55.0

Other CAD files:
Hardware/CAD/Elektrobox.stl
Hardware/CAD/AufsatzMotor.stl
Hardware/CAD/blender/TurmVorne.stl
Hardware/CAD/HalterungMotor.stl
Hardware/CAD/blender/TurmHinten.stl
Hardware/CAD/blender/TurmRechts.stl
Hardware/CAD/HalterungTeil2.stl
Hardware/CAD/Rubinator3000.stl

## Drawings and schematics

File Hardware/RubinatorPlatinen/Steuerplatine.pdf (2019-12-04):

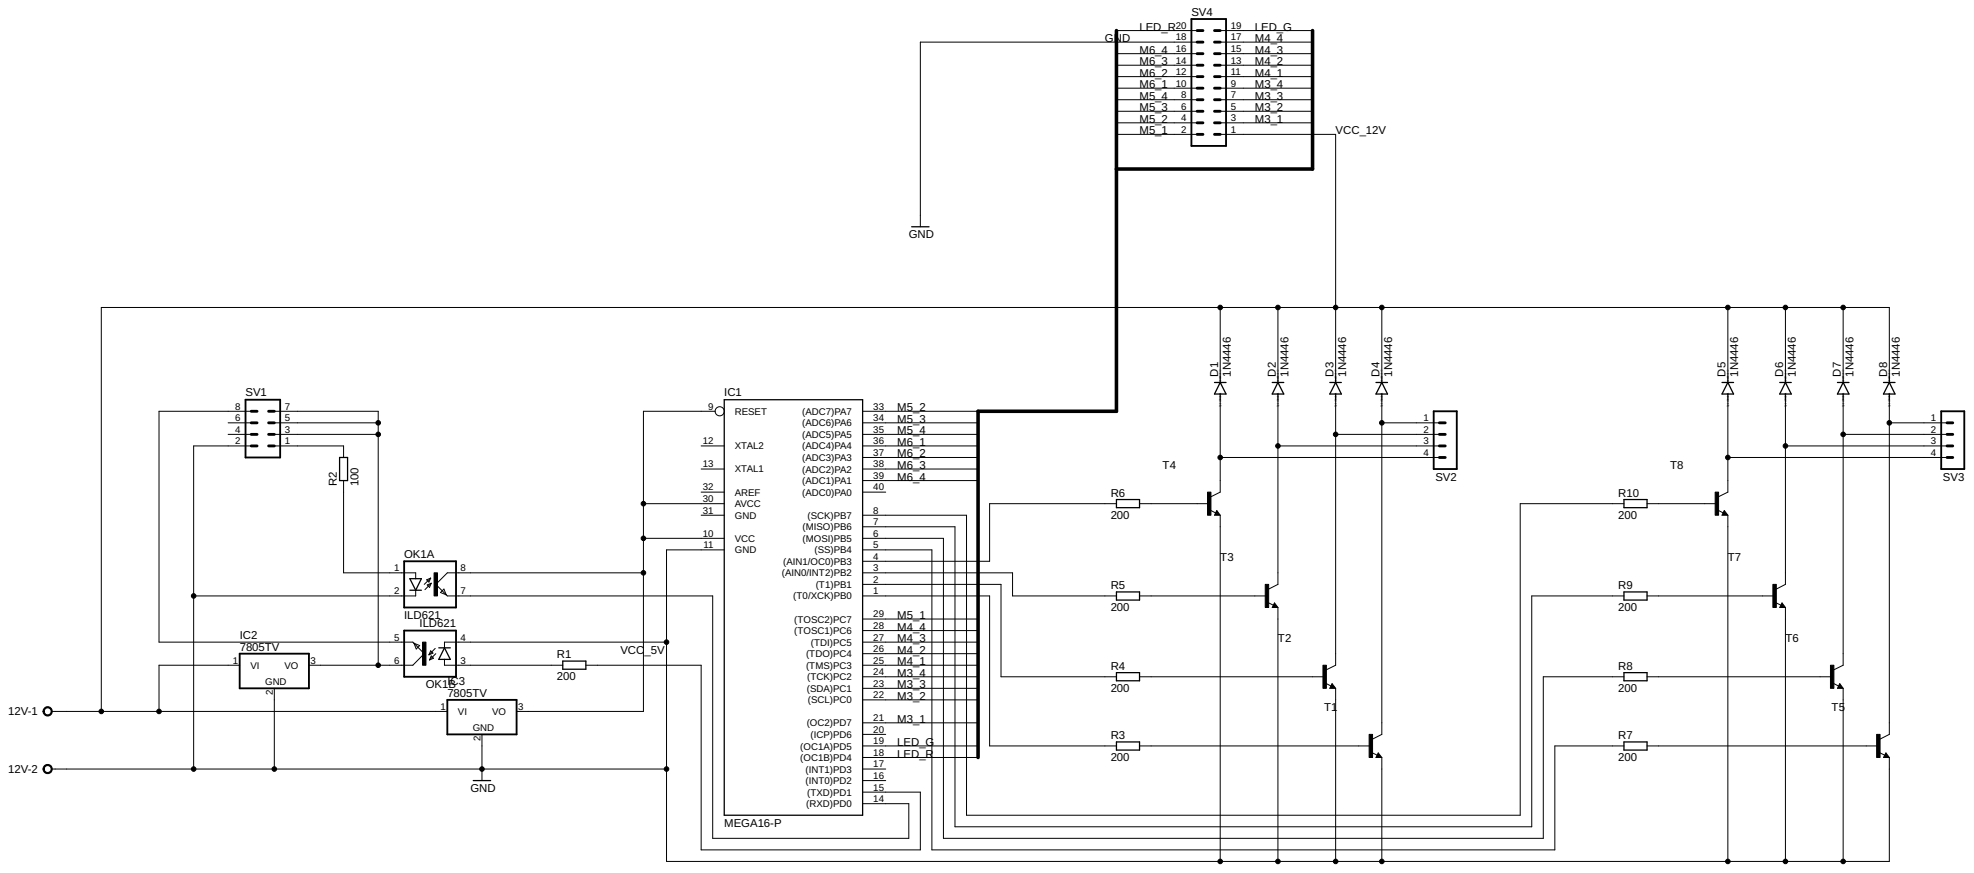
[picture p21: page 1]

SpiceOrder 1 SpiceOrder 2 SpiceOrder 1 SpiceOrder 2 SpiceOrder 1 SpiceOrder 2 SpiceOrder 1 SpiceOrder 2 SpiceOrder 1 SpiceOrder 2 SpiceOrder 1 SpiceOrder 2 SpiceOrder 1 SpiceOrder 2 SpiceOrder 1 SpiceOrder 2 MEGA16-P GND ILD621 ILD621 200 100 200 200 200 200 1N4446 1N4446 1N4446 1N4446 200 200 200 200 1N4446 1N4446 1N4446 1N4446 GND 7805TV 7805TV (ADC7)PA7 33 (ADC6)PA6 34 (ADC5)PA5 35 (ADC4)PA4 36 (ADC3)PA3 37 (ADC2)PA2 38 (ADC1)PA1 39 (ADC0)PA0 40 (SCK)PB7 8 (MISO)PB6 7 (MOSI)PB5 6 (SS)PB4 5 (AIN1/OC0)PB3 4 (AIN0/INT2)PB2 3 (T1)PB1 2 (T0/XCK)PB0 1 (TOSC2)PC7 29 (TOSC1)PC6 28 (TDI)PC5 27 (TDO)PC4 26 (TMS)PC3 25 (TCK)PC2 24 (SDA)PC1 23 (SCL)PC0 22 GND 31 AVCC 30 AREF 32 XTAL1 13 XTAL2 12 VCC 10 GND 11 RESET 9 (RXD)PD0 14 (TXD)PD1 15 (INT0)PD2 16 (INT1)PD3 17 (OC1B)PD4 18 (OC1A)PD5 19 (ICP)PD6 20 (OC2)PD7 21 IC1 12V-1 12V-2 135 2468 7 SV1 12 78 OK1A 3 5 4 6 OK1B R1 R2 T1 T2 T3 T4 R3 R4 R5 R6 D1 D2 D3 D4 1234 SV2 T5 T6 T7 T8 R7 R8 R9 R10 D5 D6 D7 D8 1234 SV3 135 246 79 810 111315 121416 1719 1820 SV4 GND VI 1 2 VO 3 IC2 GND VI 1 2 VO 3 IC3 VCC_12V GND VCC_5V M6_4 M6_4 M6_3 M6_3 M6_2 M6_2 M6_1 M6_1 M5_4 M5_4 M5_3 M5_3 M5_2 M5_2 M5_1 M5_1 M4_4 M4_4 M4_3 M4_3 M4_2 M4_2 M4_1 M4_1 M3_4 M3_4 M3_3 M3_3 M3_2 M3_2 M3_1 M3_1 LED_R LED_R LED_G LED_G

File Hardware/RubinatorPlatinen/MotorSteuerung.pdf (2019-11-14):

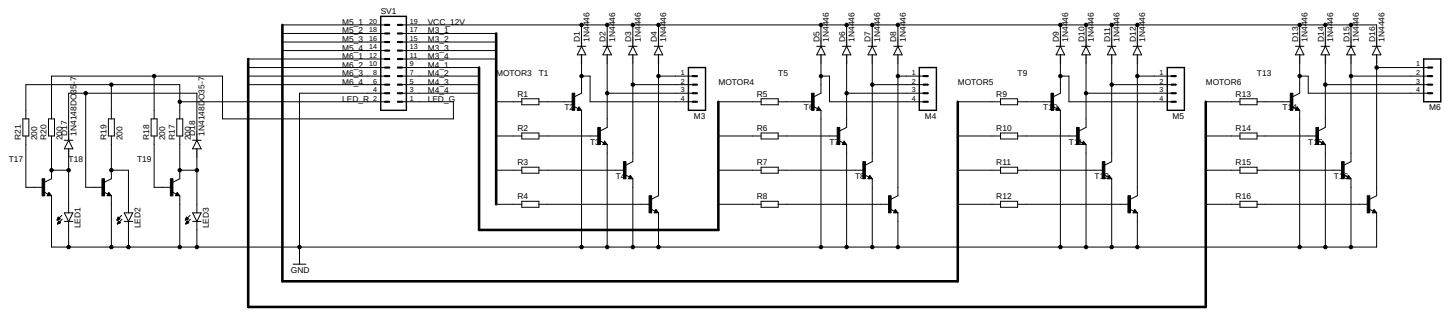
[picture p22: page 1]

SpiceOrder 1 SpiceOrder 2 SpiceOrder 1 SpiceOrder 2 SpiceOrder 1 SpiceOrder 2 SpiceOrder 1 SpiceOrder 2 SpiceOrder 1 SpiceOrder 2 SpiceOrder 1 SpiceOrder 2 SpiceOrder 1 SpiceOrder 2 SpiceOrder 1 SpiceOrder 2 SpiceOrder 1 SpiceOrder 2 SpiceOrder 1 SpiceOrder 2 SpiceOrder 1 SpiceOrder 2 SpiceOrder 1 SpiceOrder 2 SpiceOrder 1 SpiceOrder 2 SpiceOrder 1 SpiceOrder 2 SpiceOrder 1 SpiceOrder 2 SpiceOrder 1 SpiceOrder 2 SpiceOrder 1 SpiceOrder 2 SpiceOrder 1 SpiceOrder 2 GND 1N4446 1N4446 1N4446 1N4446 1N4446 1N4446 1N4446 1N4446 1N4446 1N4446 1N4446 1N4446 1N4446 1N4446 1N4446 1N4446 200 200 200 200 2001N4148DO35-7 1N4148DO35-7 135 246 79 810 111315 121416 1719 1820 SV1 D1 D2 D3 D4 T1 T2 T3 T4 R1 R2 R3 R4 D5 D6 D7 D8 T5 T6 T7 T8 R5 R6 R7 R8 D9 D10 D11 D12 T9 T10 T11 T12 R9 R10 R11 R12 D13 D14 D15 D16 T13 T14 T15 T16 R13 R14 R15 R16 LED1 LED2 LED3 T17 T18 T19 R17 R18 R19 R20 R21 D17 D18 1234 M3 1234 M4 1234 M5 1234 M6 MOTOR3 MOTOR4 MOTOR5 MOTOR6 VCC_12V M3_1 M3_2 M3_3 M3_4 M4_1 M4_2 M4_3 M4_4 LED_G M5_1 M5_2 M5_3 M5_4 M6_1 M6_2 M6_3 M6_4 LED_R

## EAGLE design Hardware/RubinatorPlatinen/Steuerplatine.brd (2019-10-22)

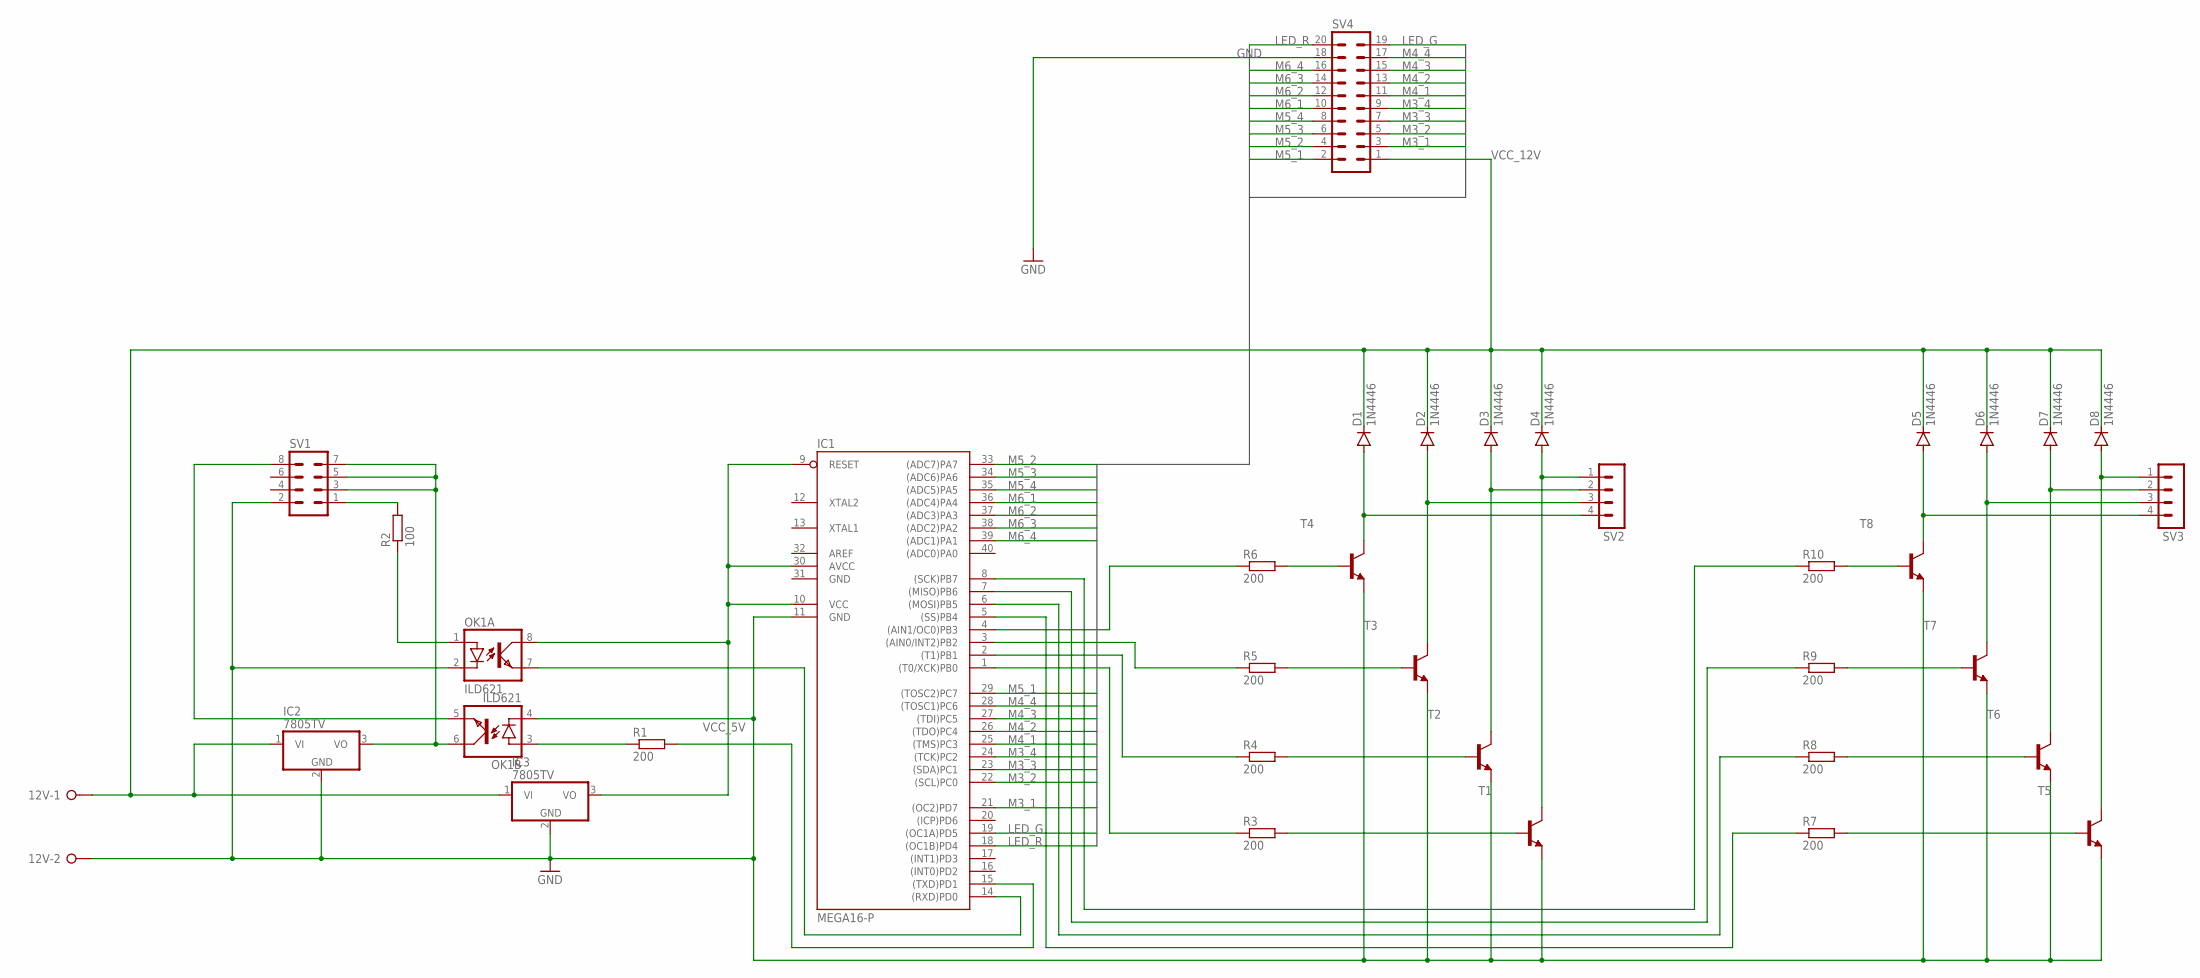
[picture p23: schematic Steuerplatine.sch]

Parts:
12V: W237-02P; W237-132
D1, D2, D3, D4, D5, D6, D7, D8: 1N4446; DO35-10
IC1: MEGA16-P; DIL40
IC2, IC3: 7805TV; TO220V
OK1: ILD621; DIL08
R1, R3, R4, R5, R6, R7, R8, R9, R10: 200; 0207/10
R2: 100; 0207/10
SV1: MA04-2
SV2, SV3: MA04-1
SV4: MA10-2
T1, T2, T3, T4, T5, T6, T7, T8: -NPN-TO126V; TO126V

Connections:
GND: 12V.2, IC1.11 (GND), IC1.31 (GND), IC2.2 (GND), IC3.2 (GND), OK1.2 (C), OK1.4 (C), SV1.2, SV4.18, T1.1 (E), T2.1 (E), T3.1 (E), T4.1 (E), T5.1 (E), T6.1 (E), T7.1 (E), T8.1 (E)
LED_G: IC1.19 ((OC1A)PD5), SV4.19
LED_R: IC1.18 ((OC1B)PD4), SV4.20
M3_1: IC1.21 ((OC2)PD7), SV4.3
M3_2: IC1.22 ((SCL)PC0), SV4.5
M3_3: IC1.23 ((SDA)PC1), SV4.7
M3_4: IC1.24 ((TCK)PC2), SV4.9
M4_1: IC1.25 ((TMS)PC3), SV4.11
M4_2: IC1.26 ((TDO)PC4), SV4.13
M4_3: IC1.27 ((TDI)PC5), SV4.15
M4_4: IC1.28 ((TOSC1)PC6), SV4.17
M5_1: IC1.29 ((TOSC2)PC7), SV4.2
M5_2: IC1.33 ((ADC7)PA7), SV4.4
M5_3: IC1.34 ((ADC6)PA6), SV4.6
M5_4: IC1.35 ((ADC5)PA5), SV4.8
M6_1: IC1.36 ((ADC4)PA4), SV4.10
M6_2: IC1.37 ((ADC3)PA3), SV4.12
M6_3: IC1.38 ((ADC2)PA2), SV4.14
M6_4: IC1.39 ((ADC1)PA1), SV4.16
unnamed: R10.2, T8.3 (B)
unnamed: IC2.3 (VO), OK1.6 (COL), SV1.3, SV1.5, SV1.7
unnamed: R2.2, SV1.1
unnamed: IC1.14 ((RXD)PD0), OK1.7 (EMIT)
unnamed: IC1.15 ((TXD)PD1), R1.2
unnamed: OK1.3 (A), R1.1
unnamed: OK1.5 (EMIT), SV1.8
unnamed: OK1.1 (A), R2.1
unnamed: R6.2, T4.3 (B)
unnamed: R5.2, T3.3 (B)
unnamed: R4.2, T2.3 (B)
unnamed: R3.2, T1.3 (B)
unnamed: IC1.1 ((T0/XCK)PB0), R3.1
unnamed: IC1.2 ((T1)PB1), R4.1
unnamed: IC1.3 ((AIN0/INT2)PB2), R5.1
unnamed: IC1.4 ((AIN1/OC0)PB3), R6.1
unnamed: D3.A, SV2.2, T2.2 (C)
unnamed: D4.A, SV2.1, T1.2 (C)
unnamed: D2.A, SV2.3, T3.2 (C)
unnamed: D1.A, SV2.4, T4.2 (C)
unnamed: R9.2, T7.3 (B)
unnamed: R8.2, T6.3 (B)
unnamed: R7.2, T5.3 (B)
unnamed: D6.A, SV3.3, T7.2 (C)
unnamed: IC1.5 ((SS)PB4), R7.1
unnamed: IC1.6 ((MOSI)PB5), R8.1
unnamed: IC1.7 ((MISO)PB6), R9.1
unnamed: IC1.8 ((SCK)PB7), R10.1
unnamed: D7.A, SV3.2, T6.2 (C)
unnamed: D8.A, SV3.1, T5.2 (C)
unnamed: D5.A, SV3.4, T8.2 (C)
VCC_5V: IC1.9 (RESET), IC1.10 (VCC), IC1.30 (AVCC), IC3.3 (VO), OK1.8 (COL)
VCC_12V: 12V.1, D1.C, D2.C, D3.C, D4.C, D5.C, D6.C, D7.C, D8.C, IC2.1 (VI), IC3.1 (VI), SV4.1

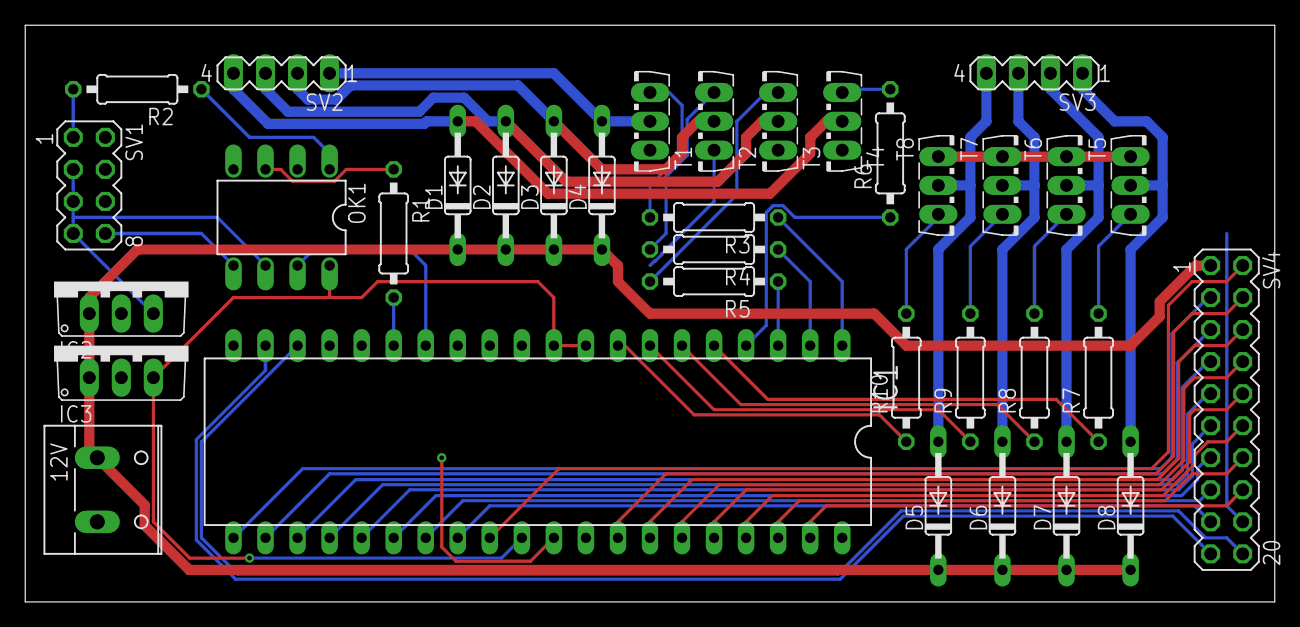
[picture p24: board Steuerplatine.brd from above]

Board: 2 copper layers, 99.1 x 45.7 mm, 35 parts (0 on the bottom side), 52 nets.

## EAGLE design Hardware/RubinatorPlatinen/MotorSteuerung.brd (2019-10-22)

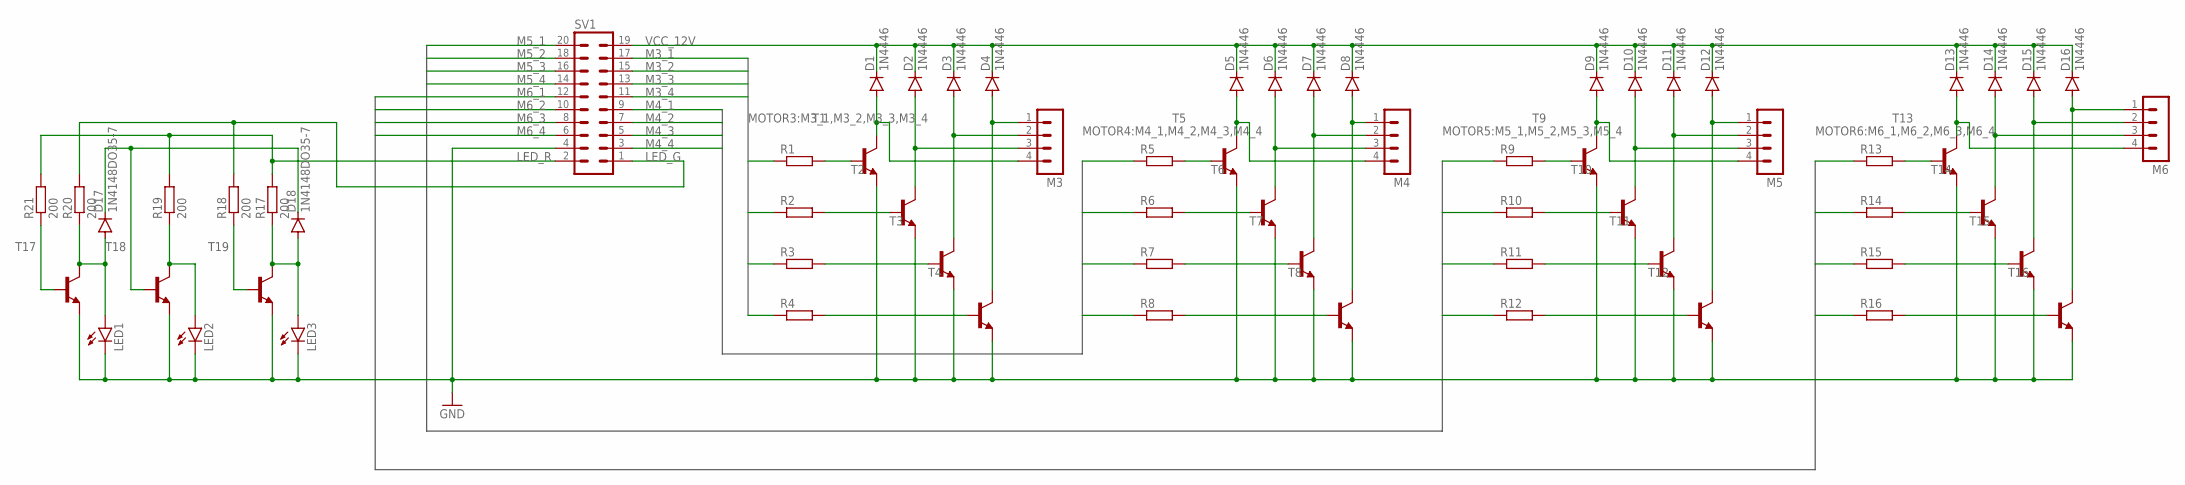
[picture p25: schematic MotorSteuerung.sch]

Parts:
D1, D2, D3, D4, D5, D6, D7, D8, D9, D10, D11, D12, D13, D14, D15, D16: 1N4446; DO35-10
D17, D18: 1N4148DO35-7; DO35-7
LED1, LED2, LED3: LED3MM
M3, M4, M5, M6: MA04-1
R1, R2, R3, R4, R5, R6, R7, R8, R9, R10, R11, R12, R13, R14, R15, R16: R-EU_0207/10; 0207/10
R17, R18, R19, R20, R21: 200; 0207/10
SV1: MA10-2
T1, T2, T3, T4, T5, T6, T7, T8, T9, T10, T11, T12, T13, T14, T15, T16: -NPN-TO126V; TO126V
T17, T18, T19: -NPN-TO92; TO92

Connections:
GND: LED1.K (C), LED2.K (C), LED3.K (C), SV1.4, T1.1 (E), T2.1 (E), T3.1 (E), T4.1 (E), T5.1 (E), T6.1 (E), T7.1 (E), T8.1 (E), T9.1 (E), T10.1 (E), T11.1 (E), T12.1 (E), T13.1 (E), T14.1 (E), T15.1 (E), T16.1 (E), T17.1 (E), T18.1 (E), T19.1 (E)
LED_G: R18.2, R20.2, SV1.1
LED_R: R17.2, R19.2, R21.2, SV1.2
M3_1: R1.1, SV1.17
M3_2: R2.1, SV1.15
M3_3: R3.1, SV1.13
M3_4: R4.1, SV1.11
M4_1: R5.1, SV1.9
M4_2: R6.1, SV1.7
M4_3: R7.1, SV1.5
M4_4: R8.1, SV1.3
M5_1: R9.1, SV1.20
M5_2: R10.1, SV1.18
M5_3: R11.1, SV1.16
M5_4: R12.1, SV1.14
M6_1: R13.1, SV1.12
M6_2: R14.1, SV1.10
M6_3: R15.1, SV1.8
M6_4: R16.1, SV1.6
unnamed: D1.A, M3.4, T1.2 (C)
unnamed: D2.A, M3.3, T2.2 (C)
unnamed: D3.A, M3.2, T3.2 (C)
unnamed: D4.A, M3.1, T4.2 (C)
unnamed: R1.2, T1.3 (B)
unnamed: R2.2, T2.3 (B)
unnamed: R3.2, T3.3 (B)
unnamed: R4.2, T4.3 (B)
unnamed: D5.A, M4.4, T5.2 (C)
unnamed: D6.A, M4.3, T6.2 (C)
unnamed: D7.A, M4.2, T7.2 (C)
unnamed: D8.A, M4.1, T8.2 (C)
unnamed: R5.2, T5.3 (B)
unnamed: R6.2, T6.3 (B)
unnamed: R7.2, T7.3 (B)
unnamed: R8.2, T8.3 (B)
unnamed: D9.A, M5.4, T9.2 (C)
unnamed: D10.A, M5.3, T10.2 (C)
unnamed: D11.A, M5.2, T11.2 (C)
unnamed: D12.A, M5.1, T12.2 (C)
unnamed: R9.2, T9.3 (B)
unnamed: R10.2, T10.3 (B)
unnamed: R11.2, T11.3 (B)
unnamed: R12.2, T12.3 (B)
unnamed: D13.A, M6.4, T13.2 (C)
unnamed: D14.A, M6.3, T14.2 (C)
unnamed: D15.A, M6.2, T15.2 (C)
unnamed: D16.A, M6.1, T16.2 (C)
unnamed: R13.2, T13.3 (B)
unnamed: R14.2, T14.3 (B)
unnamed: R15.2, T15.3 (B)
unnamed: R16.2, T16.3 (B)
unnamed: D18.A, LED3.A, R17.1, T19.3 (C)
unnamed: LED2.A, R19.1, T18.3 (C)
unnamed: D17.A, LED1.A, R20.1, T17.3 (C)
unnamed: D17.C, D18.C, T18.2 (B)
unnamed: R21.1, T17.2 (B)
unnamed: R18.1, T19.2 (B)
VCC_12V: D1.C, D2.C, D3.C, D4.C, D5.C, D6.C, D7.C, D8.C, D9.C, D10.C, D11.C, D12.C, D13.C, D14.C, D15.C, D16.C, SV1.19

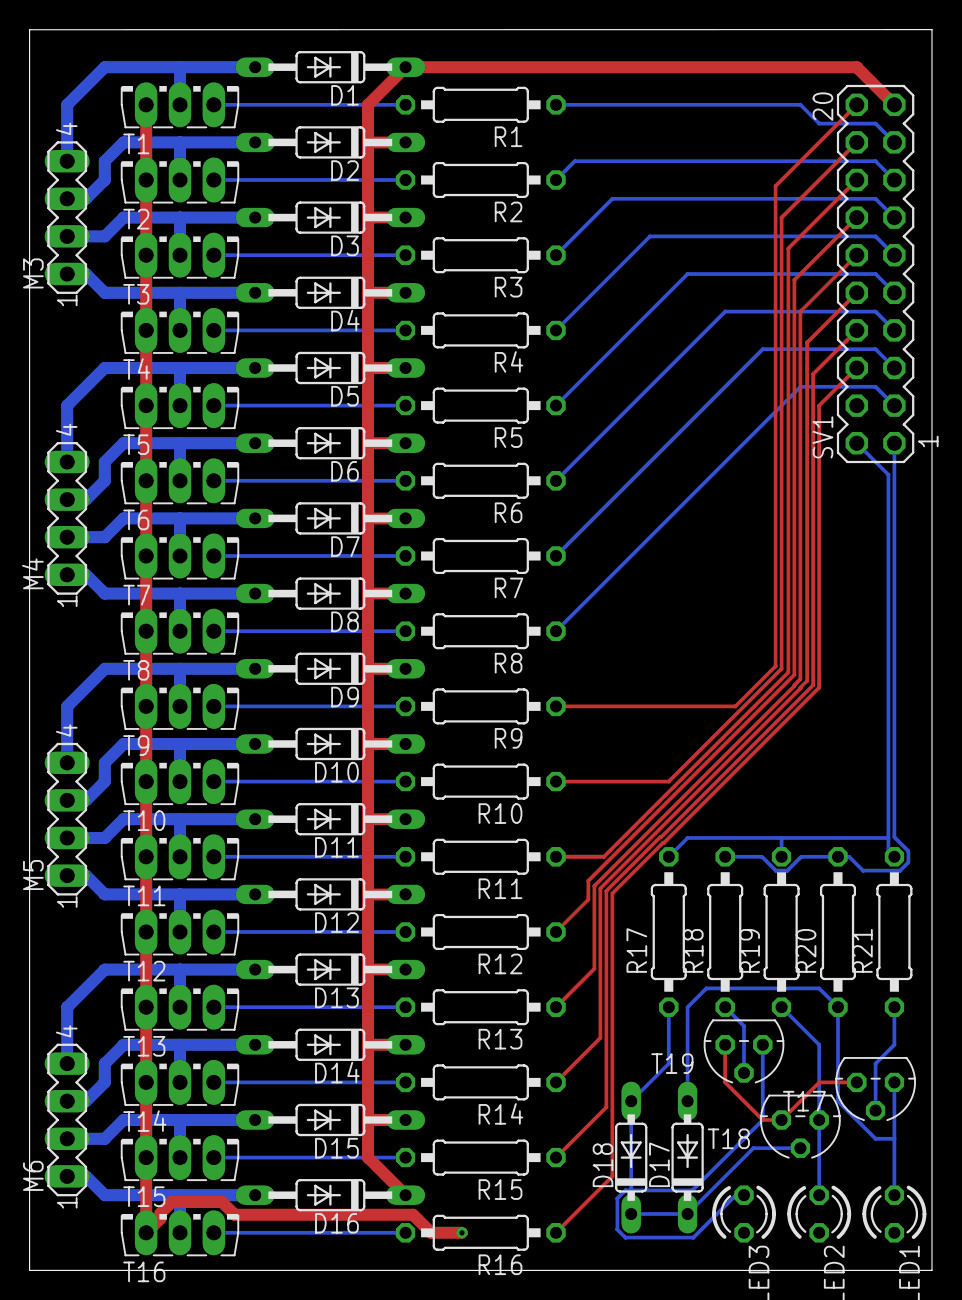
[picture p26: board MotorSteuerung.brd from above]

Board: 2 copper layers, 61.0 x 83.8 mm, 66 parts (0 on the bottom side), 58 nets.

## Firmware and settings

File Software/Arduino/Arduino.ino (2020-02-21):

#include "stepper.h"

#define STATE_DISCONNECT 0x00
#define STATE_CONNECT 0x01
#define STATE_SOLVED 0x02

int stepperPins[6][4] = {
    { 26, 28, 22, 24 },
    { 23, 25, 27, 29 },
    { 36, 38, 32, 34 },
    { 33, 35, 37, 39 },
    { 42, 44, 46, 48 },
    { 47, 49, 43, 45 }
};


Stepper steppers[6];

int state;
int ledGreen = 3;
int ledRed = 2;

int ledsUp = 4;
int ledsDown = 5;
int ledStripes = 6;

void setup() {
	for(int i = 0; i < 6; i++) {
    steppers[i] = Stepper(stepperPins[i]);
  }

  pinMode(ledGreen, OUTPUT);  
  pinMode(ledRed, OUTPUT);

  // testing status leds
  digitalWrite(ledGreen, LOW);
  digitalWrite(ledRed, HIGH);

  delay(500);
  digitalWrite(ledGreen, HIGH);

  delay(500);
  digitalWrite(ledRed, LOW);

  delay(500);
  digitalWrite(ledRed, HIGH);
  digitalWrite(ledGreen, LOW);

  pinMode(ledsUp, OUTPUT);
  digitalWrite(ledsUp, LOW);
  pinMode(ledsDown, OUTPUT);
  digitalWrite(ledsDown, LOW);
  pinMode(ledStripes, OUTPUT);
  digitalWrite(ledStripes, LOW);

  Serial.begin(9600);

	// 2 minutes timeout
	Serial.setTimeout(120000);
	digitalWrite(ledRed, HIGH);
}

void loop() {
  // put your main code here, to run repeatedly:

	if (Serial.available()) {
	  uint8_t data = Serial.read();

  	// disconnected
	  if (data == -1) {
		  stateCommand(STATE_DISCONNECT);
		  return;
	  }

    switch (data & 0xF0) {
      case 0xA0:    // states
        stateCommand(data & 0xF);
        break;
      case 0x00:    // move
        handleMove(data);
        break;
      case 0x10:    // multiTurn
        handleMultiTurnMove(data);
        break;
      case  0x40:   // leds
        while (!Serial.available()) ;
        uint8_t brightness = Serial.read();
        ledCommand(data & 0x0F, brightness);
        break;
    }
  }
}

void stateCommand(uint8_t newState) {
  if(state != newState) {

    switch(newState) {
      case STATE_DISCONNECT:
        state = STATE_DISCONNECT;

        digitalWrite(ledGreen, LOW);
        digitalWrite(ledRed, HIGH);

        // set all leds off
        digitalWrite(ledsDown, 0);
        digitalWrite(ledsUp, 0);
        digitalWrite(ledStripes, 0);
        break;
      case STATE_CONNECT:
        state = STATE_CONNECT;

        digitalWrite(ledGreen, HIGH);
        digitalWrite(ledRed, HIGH);        
        break;
      case STATE_SOLVED:
        state = STATE_SOLVED;

        digitalWrite(ledGreen, HIGH);
        digitalWrite(ledRed, LOW);
        break;
    }
  }
  
  Serial.write(0xF0 | state);
}

void handleMove(uint8_t move) {  
  if(state != STATE_CONNECT) {
    Serial.write(0xB1);  // send not connected
    return;
  }  

  uint8_t face = (move >> 1) - 1;
  bool isPrime = move & 0x01;

  if(face < 6) {
    int steps = (1 + (-2 * isPrime)) * 50;
    steppers[face].doMove(steps, 5);

    Serial.write(0x20 + move);
  }
  else {
    Serial.write(0xB2);  // send not valid
  }
}

void handleMultiTurnMove(uint8_t multiTurnMove) {
  if(state != STATE_CONNECT) {
    Serial.write(0xB1);  // send not connected
    return;
  }

  int axis = (multiTurnMove & (1 << 3 | 1 << 2)) >> 2;

  if(axis < 3) {
    Serial.write(axis);

    int leftDir = (multiTurnMove & (1 << 1)) >> 1;
    int rightDir = multiTurnMove & (1 << 0);

    leftDir = leftDir == 0 ? 1 : -1;
    rightDir = rightDir == 0 ? 1 : -1;

    Serial.write(leftDir);
    Serial.write(rightDir);

    doMultiTurnMove(axis, leftDir, rightDir, 5);

    Serial.write(0x20 + multiTurnMove);
  }
  else {
    Serial.write(0xB2);  // send not valid
  }
}

void doMultiTurnMove(int axis, int leftDir, int rightDir, const int stepDelay) {
  int rightSteppers[] = {4, 3, 5};
  int rightStepper = rightSteppers[axis];
  int leftStepper = axis;

  for(int i = 0; i < 50; i++) {
    steppers[leftStepper].doStep(leftDir, 0);
    steppers[rightStepper].doStep(rightDir, 0);

    delay(stepDelay);
  }

  steppers[leftStepper].writeState(0, 0, 0, 0);
  steppers[rightStepper].writeState(0, 0, 0, 0);
}

void ledCommand(uint8_t command, uint8_t brightness) {    
  if(command & 0x01 == 0x01) {
    // leds down
    analogWrite(ledsDown, brightness);    
  }

  if(command & 0x02 == 0x02) {
    // leds up
    analogWrite(ledsUp, brightness);
  }

  if(command & 0x04 == 0x04) {
    // led stripes
    analogWrite(ledStripes, brightness);
  }

  Serial.write(command);
  Serial.write(brightness);
}

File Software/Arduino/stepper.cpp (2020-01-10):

#include "stepper.h"
#include "Arduino.h"

Stepper::Stepper() {
    
}

Stepper::Stepper(int *pins) {
    count = 500;

    for(int i = 0; i < 4; i++) {
        this->pins[i] = pins[i];

        pinMode(pins[i], OUTPUT);
        digitalWrite(pins[i], LOW);
    }
}

void Stepper::writeState(int p0, int p1, int p2, int p3) const {
    digitalWrite(pins[0], p0);
    digitalWrite(pins[1], p1);
    digitalWrite(pins[2], p2);
    digitalWrite(pins[3], p3);
}

void Stepper::doMove(int steps, const int stepDelay) {
    int dir = steps < 0 ? -1 : 1;
    steps = abs(steps);

    for(int i = 0; i < steps; i++) {
        count += dir;

        switch(count % 4) {
            case 0:     writeState(0, 1, 1, 0); break;
            case 1:     writeState(0, 1, 0, 1); break;
            case 2:     writeState(1, 0, 0, 1); break;
            case 3:     writeState(1, 0, 1, 0); break;
        }

        if(count < 10)
            count += 100;
        else if(count > 1000)
            count %= 4;

        delay(stepDelay);
    }
    writeState(0, 0, 0, 0);
}

void Stepper::doStep(int direction, int timeout = 0) {
    count += direction; 

    switch(count % 4) {
        case 0:     writeState(0, 1, 1, 0); break;
        case 1:     writeState(0, 1, 0, 1); break;
        case 2:     writeState(1, 0, 0, 1); break;
        case 3:     writeState(1, 0, 1, 0); break;
    }

    if(count < 10)
        count += 100;
    else if(count > 1000)
        count %= 4;

    delay(timeout);    
}

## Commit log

2019-08-21 GITIGNORE und GITATTRIBUTES hinzufügen.
2019-08-23 Proting to .Net Framework
2019-08-23 Porting to .Net Framework 4.7.2
2019-08-28 Fix shuffle rendering in animation thread
2019-09-21 Add Arduino communication
2019-09-25 camera exception handling
2019-09-27 more efficent camera stream
2019-10-05 Make window context current
2019-10-07 Performance increase on animation thread (made into a task)
2019-10-08 Work on Last Layer Solving
    [PllPatternGenerator.xlsx]
2019-10-22 Add some unnecessary stuff
    [MotorSteuerung.brd, MotorSteuerung.sch, Steuerplatine.brd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]
2019-10-27 Add 3D Model
    [Bodenplatte.stl, Gestell_Neu.FCStd]
2019-10-27 Add actual 3D files
    [Gestell_Neu.FCStd]
2019-10-29 Work on 3D Model
    [Bodenplatte.stl, Gestell_Neu.FCStd, HalterungTeil1.stl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]
2019-11-05 Implement 'Eagle' Case
    [FTLCases.xlsx, HalterungTeile.FCStd]
2019-11-05 Add components list
    [Bauteile.xlsx]
2019-11-06 Work on FTL
    [FTLCases.xlsx]
2019-11-06 update partslist
    [Bauteile.xlsx]
2019-11-14 Work on F2L
    [Bauteile.xlsx, Gestell_Neu.FCStd, HalterungTeil3.stl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]
2019-11-15 Implement F2L cases Corner false in slot
2019-11-17 Add E-Box and Drawings
    [Gestell_Neu.FCStd, HalterungTeile.FCStd, Rubinator3000.FCStd]
2019-11-18 Add Motorhalterungen
    [HalterungMotor.stl, Rubinator3000.FCStd]
2019-11-18 Add WiFi program
    [Bodenplatte.stl, HalterungMotor.stl, HalterungTeil1.stl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]
2019-11-19 Add new MotorHalterungen
    [AufsatzMotor.stl, AufsatzMotorAussparung.stl, Rubinator3000.FCStd]
2019-11-26 compile arduino program
2019-11-28 Make Solving async and work on last layer solving
    [PllPatternGenerator.xlsx]
2019-12-02 Add log Thread
2019-12-02 Work on microcontroller communication
    [MotorController.componentinfo.xml]
2019-12-04 Add communication protocol
    [MotorController.componentinfo.xml]
2019-12-09 Add IO support on ATMEGA16
    [MotorController.componentinfo.xml]
2019-12-09 implement Serial
    [MotorController.componentinfo.xml]
2019-12-13 Add IO and Serial communication
    [MotorController.componentinfo.xml]
2019-12-15 CAD Stuff
    [AntriebUnten.stl, Antriebuten.stl, Elektrobox.stl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]
2019-12-15 Add Software Folder
    [Rubinator3000.FCStd]
2019-12-16 Implement Arduino Mega for 'MINT-Messe'
2019-12-18 Fix Problems for 'MINT-Messe'
    [Arduino.ino, stepper.cpp]
2019-12-20 Added MoveSynchronization and wrapped arduino
2019-12-21 Finished graphics error and logThread joining, introduced timeout on arduino
    [Arduino.ino]
2019-12-27 Fix cube solving algorithm
    [FTLCases.xlsx]
2020-01-04 Fix .csproj and optimize face rotation
    [PllPatternGenerator.xlsx]
2020-01-08 define Camera
2020-01-08 Add arduino multi turns
2020-01-08 Camera and PieChart fixes
2020-01-10 Fix Arduinoprogram
2020-01-10 Fix multiturn steppers
2020-01-14 Manual Cube Generation From Camera-Streams and GUI-Name-Refactoring
2020-01-26 Adding Camera - not working yet
2020-01-27 CameraPreview Stuff
2020-01-29 Add bluetooth device selection
2020-01-30 Add bluetooth server and connect button
2020-02-02 Wire up bluetooth control backend
2020-02-12 Arduino responses and color values
2020-02-12 GUI and LEDs
2020-02-14 Fix Arduino and other stuff
    [Arduino.ino]
2020-02-21 Reduce arduino step delay
